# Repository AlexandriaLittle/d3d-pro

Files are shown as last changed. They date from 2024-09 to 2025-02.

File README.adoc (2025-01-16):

= D3D Pro 3D Printer

=== https://alexandrialittle.github.io/d3d-pro/[Click HERE for the Documentation Page!]

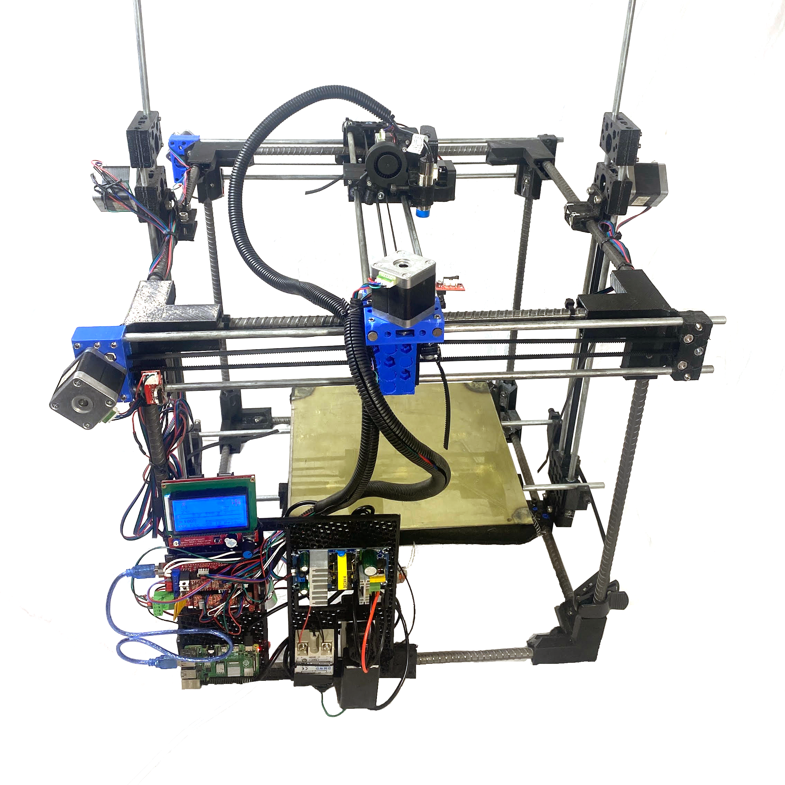
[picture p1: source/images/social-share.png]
D3D Pro 3D Printer


== How to use this project:
All of the files needed to produce the machine are in the 'source' folder. This includes the STLs for printing, the purchase list, and the firmware source code. The instructions are available https://alexandrialittle.github.io/d3d-pro/[HERE].

Modeled in Legacy DOF (Distributed Open Source Hardware Framework)

== Frequently Asked Questions:

=== Who is this printer for? Why should I build this printer?
- This printer is designed for the hobbyist, the "prosumer", and anyone who needs industrial productivity on a small scale. The D3D Pro 3D Printer is designed to be user repairable for life - i.e. not planned obsolesence / planned failure. It is made entirely from common-off-the-shelf components so that sourcing the materials for the build and for repair is easy and quick. If you need a machine that can last you your entire life, this is the one for you!

=== What features does the D3D Pro have? What is it capable of?
* The D3D Pro has automatic bed leveling, printing over WIFI, advanced Marlin firmware features including Input Shaping and Linear (Pressure) Advance, a gearless extruder with an open filament path, superior performance with flexable filaments (due to the short distance between filament drive point and melt zone), a standardized Universal Axis motion system, and much more.
* The D3D Pro is capable of printing strong, industrial quality parts quickly with good print precision and robust performance.

=== What is the print volume?
* The D3D Pro printer has a 300mm x 300mm x 350mm print volume. Is that not enough for your needs? The printer is also fully scalable!

=== What does "modular" mean for this 3D Printer?
* The D3D Pro is broken up into six modules - The Univeral Axis, the Universal Frame, the Universal Controller, the Universal Gearless Extruder, the Fast Heated Bed, and the Filament Spool Holder. These modules can be used for many things beyond just a 3D Printer, including other CNC machines, camera sliders, a personal computer, a robot controller, a miltipurpose heated surface, and more! More modules can be added to the 3D Printer to increase its performance capabilities. For example, more Universal Axes can be added to increase bed lift, additional Universal Controllers and Universal Gearless Extruders can be added for higher throughput, etc.

=== What does "fully scalable" mean for this printer?
* Because the printer uses standardized modular components, it can be modified to be much larger in size if necessary for your use case. Simply increase the size of the frame, axes rods and belts, and heated bed, extend the wires, and you're all but good to go! Additional axes can be added to the printer easily to increase the bed lift capacity or provide a more rigid axis.

=== What materials can it print?
* The printer can print any 3D Printing filament of 2.85mm or 1.75mm diameter (depending on how you build the extruder) up a maximum temperature of 285C. The heated bed surface can reach a temperature of 100C+. The has been verified to work with common printer filaments like PLA, PETG, PET, and ASA.

=== Why are all of the axes belt-driven?
* The standardized Universal Axis motion system is fully belt-driven to simplify the machine's design, make maintenance a breeze, and allow for part interchangeability.

=== Why is the frame made out of rebar?
* Rebar is an inexpensive, robust, and strong material that comes in stock lengths of up to 20'. This helps the printer scale up if necessary for litte extra cost while providing a solid frame for the machine to operate in.

=== Why is the extruder "gearless"?
* The D3D Pro uses the Universal Gearless Extruder for its open filament path, making the job of clearing any possible clogs a simple task. The gearless design is also simpler, requires less maintenance, has lower cost replacement parts, and provides superior performance with soft, flexible filaments due to the short distance between the point where the filament is driven by the extruder gear and the melt zone.

=== How fast does it print?
* With the proper slicer settings and tuning of Marlin firmware's advanced features, the printer has been able to reliably print at speeds as fast as 80mm/s - 100mm/s at an acceleration of 3000mm/s^2. (0.4mm nozzle at 0.2mm layer height)

=== What is the volumetric flow rate of the hotend?
* The D3D Pro uses a Volcano style hotend, the specifications of which can be found here: https://e3d-online.com/products/volcano-hotend[E3D Volcano Hotend Product Page]

=== What are the machine dimensions?
* (675mm Wide x 665mm Deep x 645mm Tall) without the filament spool holder
* (675mm Wide x 665mm Deep x 960mm Tall) (approx.) with the filament spool holder
* (26.5" Wide x 26" Deep x 25.25" Tall) (approx.) without filament spool holder
* (26.5" Wide x 26" Deep x 37.5" Tall) (approx.) with filament spool holder

=== I want to build one! Where can I get parts and tools?
* Many of the parts for the printer can be purchased from the local hardware store. For example, you can get the fasteners, all of the heated bed components, the rebar frame members, the rods for the Universal Axes, etc. at your local Lowe's, Menards, Home Depot, etc. Some of the more specific 3D Printer components can be sourced from online retailers like Amazon, eBay, Aliexpress, etc. All of the tools should be available at the hardware store as well! Lastly, the 3D Printed components can be printed from the source files provided (if you have access to a 3D Printer already), or ordered from a 3D printing service or a friend with a printer. :)

== Contributors
 - Alexandria Little
 - Marcin Jakubowski, Ph.D.
 - Open Source Ecology
 - Nathan Heidt
 - Sean Marquez
 - J. Simmons, Ph.D.
 - Eric Lotze (One of the original 3D printer devs)
 - Irvin Inzurriaga (Wiring Video)
 - Jean-Baptiste Vervaeck (Graphic design of original documentation template)
 - Printables User @OK1HRA_5209 - https://www.printables.com/model/716371-parameterizable-rugged-box-in-openscad[Parameterizable rugged box in OpenScad] (CC-BY-SA-4.0)
 - Marlena Nedeljkovic

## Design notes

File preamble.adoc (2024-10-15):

== Thank you for reading this documentation! 
It would mean the world to all of us who poured our time, love, and efforts into this project if you would study, share, replicate, sell, remix, manufacture, mod, or otherwise interact with the D3D Pro 3D Printer. This work is released under the https://creativecommons.org/licenses/by-sa/4.0/[Creative Commons Attribution Share-Alike 4.0 International license]. Feel free to use all of the freedoms that you are granted under that (pretty damn permissive) license. Remember to credit the contributors and share your remixes and upgrades under the same license!

== Contributors
 - Alexandria Little
 - Marcin Jakubowski, Ph.D.
 - Open Source Ecology
 - Nathan Heidt
 - Sean Marquez
 - J. Simmons, Ph.D.
 - Eric Lotze (One of the original 3D printer devs)
 - Irvin Inzurriaga (Wiring Video)
 - Jean-Baptiste Vervaeck (Graphic design of original documentation template)
 - Printables User @OK1HRA_5209 - https://www.printables.com/model/716371-parameterizable-rugged-box-in-openscad[Parameterizable rugged box in OpenScad] (CC-BY-SA-4.0)
 - Marlena Nedeljkovic
 
== A note on tool substitution
There are a lot of tools listed as 'required' in this project, but many of them can be substituted for other, simpler tools. If you do not have access to all of the nice-to-have tools that are listed in this project, feel free to adapt the instructions to what you have on hand. Please remember to be safe and use common sense!

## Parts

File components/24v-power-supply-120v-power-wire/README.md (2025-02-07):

TODO: USE EITHER 18AWG OR 20AWG WIRE FOR 120v AC

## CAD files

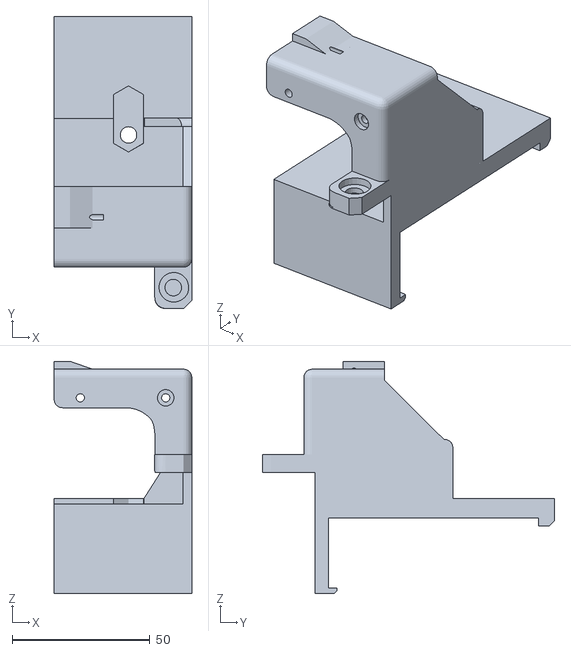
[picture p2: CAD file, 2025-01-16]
source/printed_parts/14-Extruder Main.stl
50.0 x 106.0 x 84.4

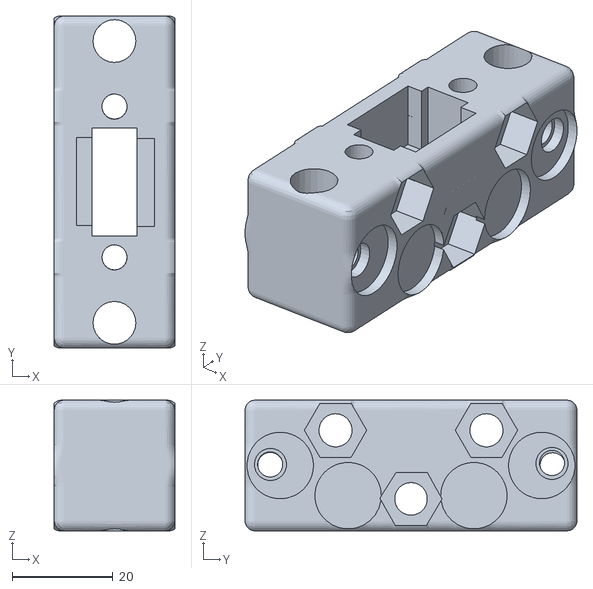
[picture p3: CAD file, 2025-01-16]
source/printed_parts/11-Idler.stl
24.0 x 66.0 x 26.0

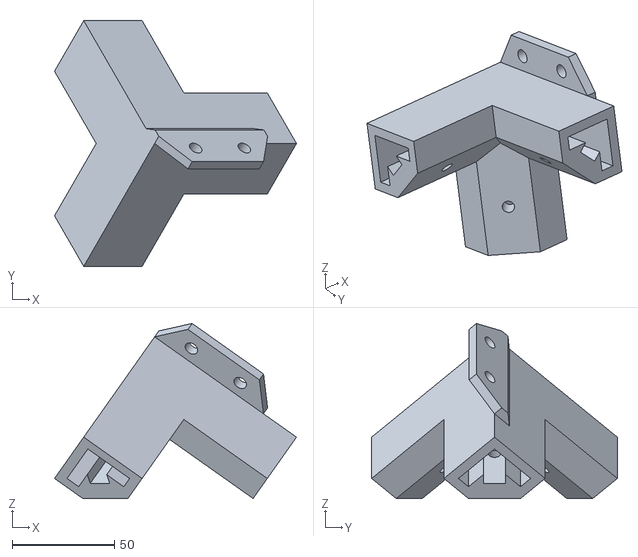
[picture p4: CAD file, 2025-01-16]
source/printed_parts/2-Corner Connector Left.stl
118.4 x 120.2 x 85.6

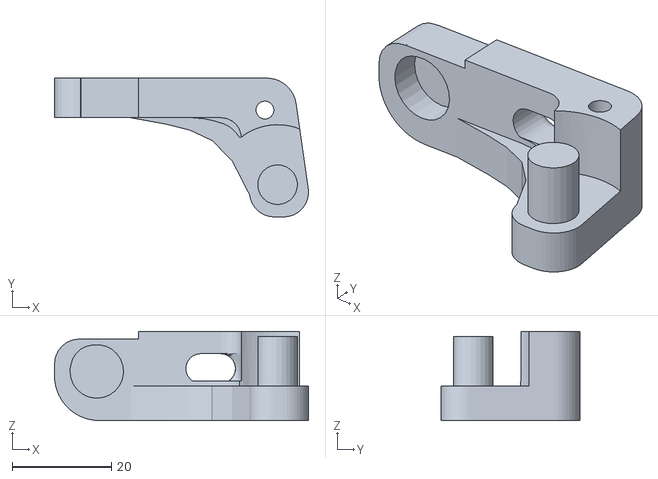
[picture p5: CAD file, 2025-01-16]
source/printed_parts/16-Extruder Tensioner.stl
51.2 x 28.0 x 18.0

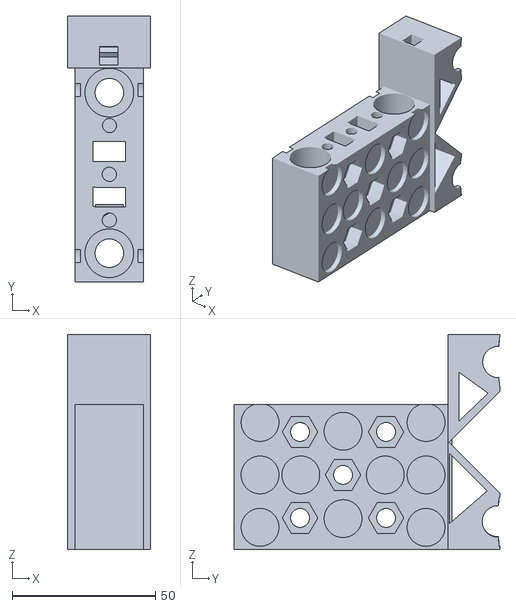
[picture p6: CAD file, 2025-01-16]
source/printed_parts/9-Y2 Carriage.stl
29.0 x 92.7 x 75.0

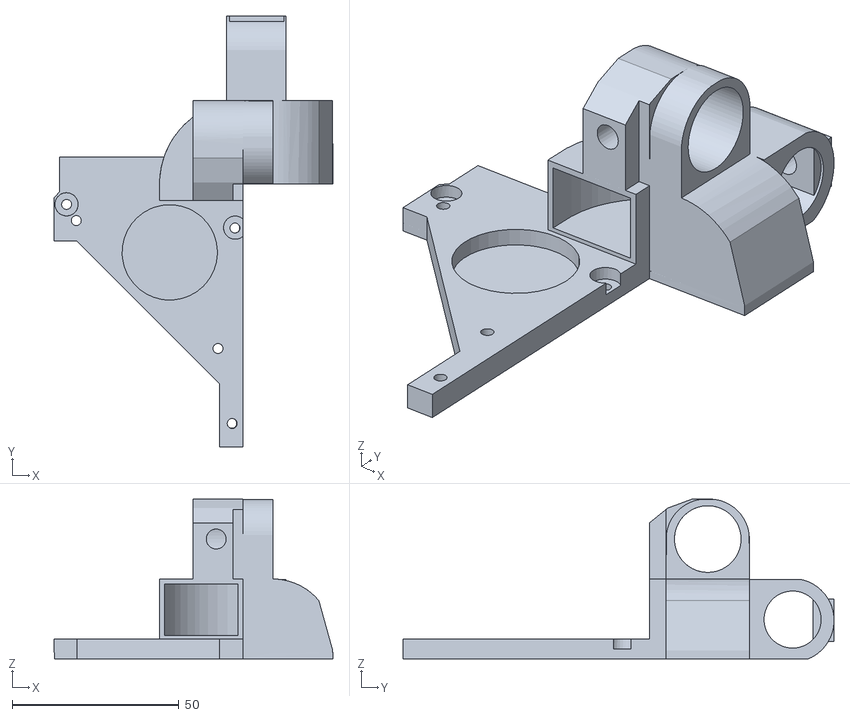
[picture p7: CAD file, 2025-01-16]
source/printed_parts/15-Extruder Secondary.stl
83.6 x 129.4 x 48.0

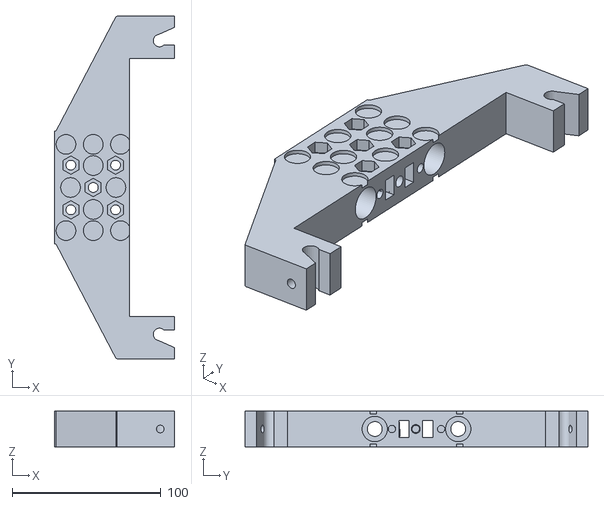
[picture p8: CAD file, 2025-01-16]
source/printed_parts/7-Z Carriage.stl
80.6 x 229.9 x 24.0

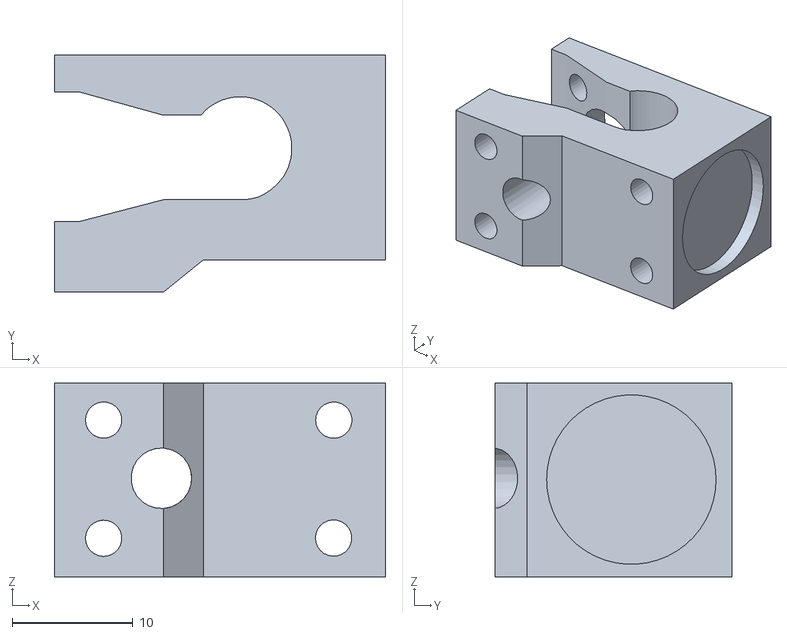
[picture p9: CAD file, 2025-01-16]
source/printed_parts/12-Autoparallel Clip.stl
27.4 x 19.6 x 16.0

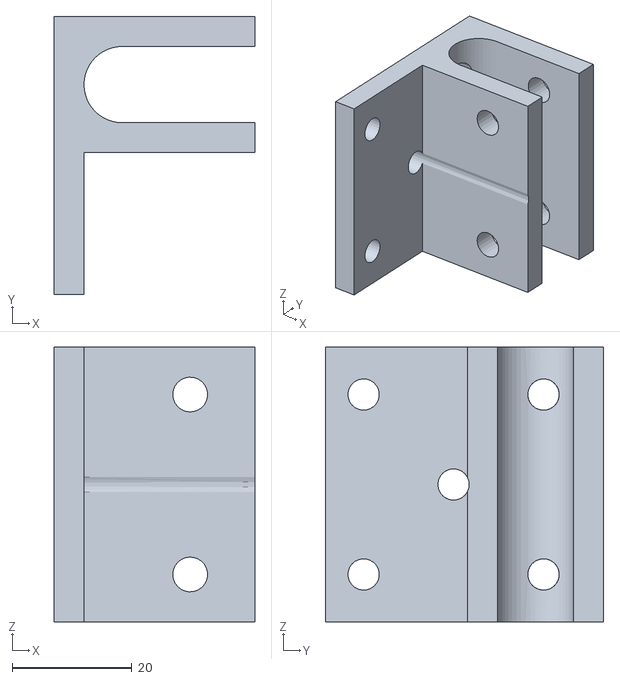
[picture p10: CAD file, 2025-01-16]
source/printed_parts/4-Universal Frame Rebar Mount.stl
33.5 x 46.4 x 45.8

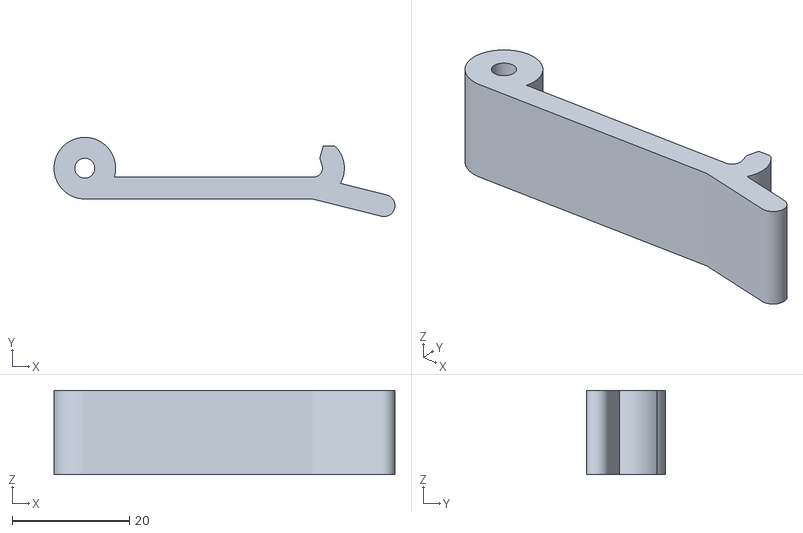
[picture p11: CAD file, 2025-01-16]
source/printed_parts/22-Control Panel Electrical Box Clip.stl
58.1 x 13.5 x 14.4

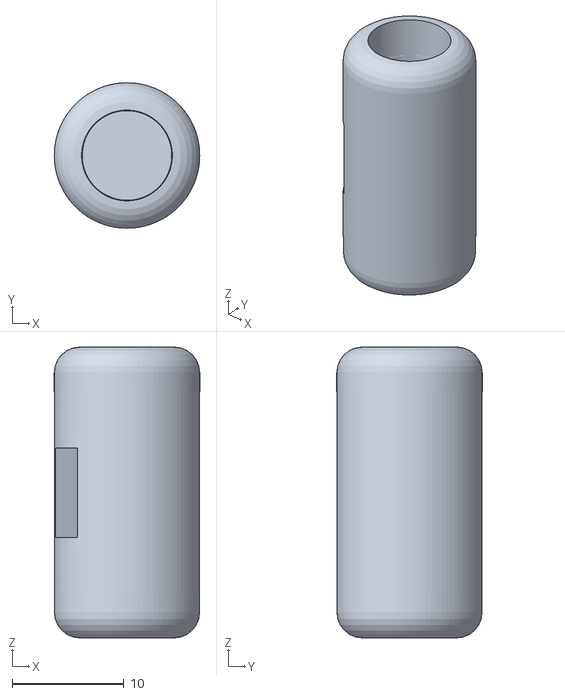
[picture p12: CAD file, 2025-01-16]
source/printed_parts/17-Belt Cylinder.stl
13.0 x 13.0 x 26.0

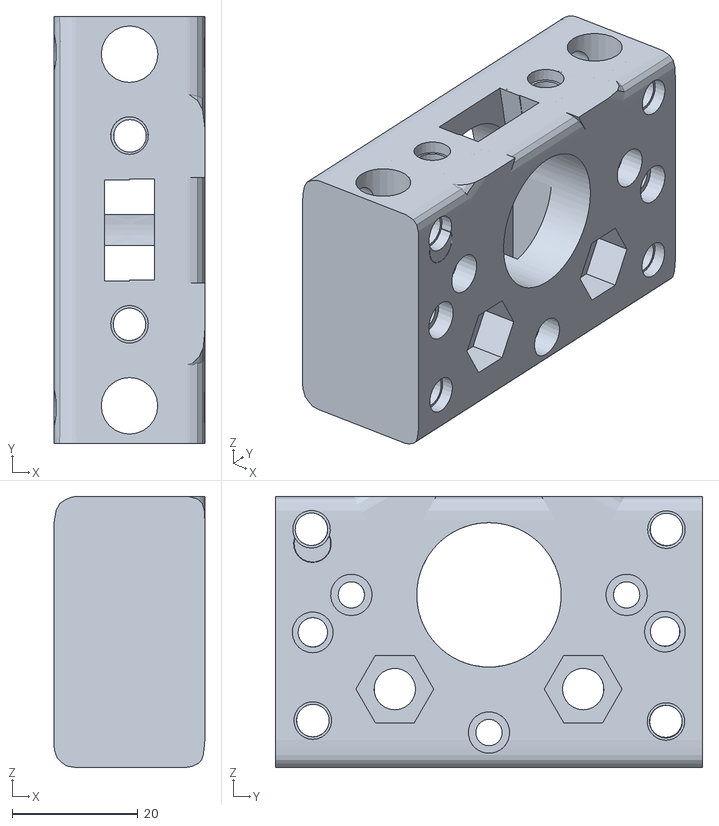
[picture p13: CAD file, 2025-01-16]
source/printed_parts/5-Motor piece.stl
24.0 x 68.0 x 43.2

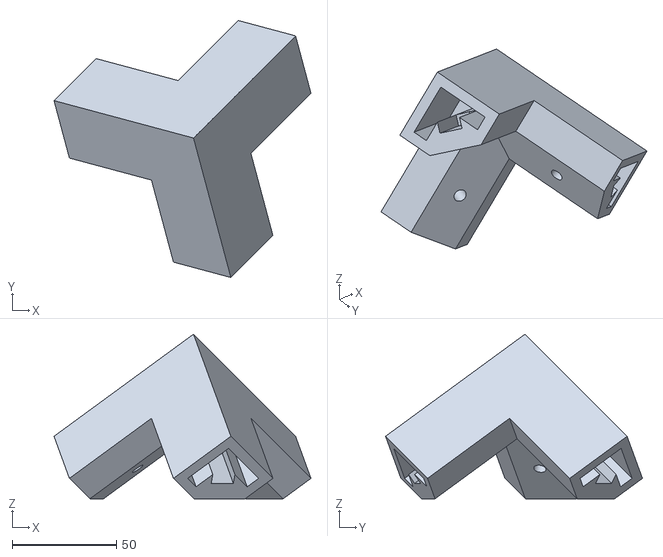
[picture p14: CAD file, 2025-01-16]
source/printed_parts/1-Corner Connector.stl
123.5 x 123.5 x 79.1

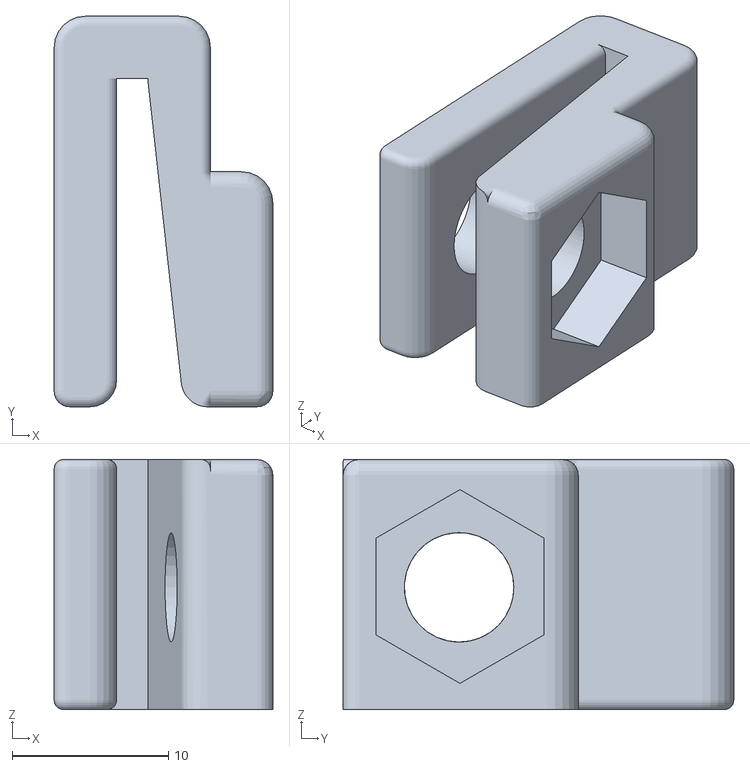
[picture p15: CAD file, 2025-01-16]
source/printed_parts/18-Belt Clamp.stl
14.0 x 25.0 x 16.0

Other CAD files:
source/printed_parts/3-Corner Connector Right.stl
source/printed_parts/8-Y1 Carriage.stl
source/printed_parts/10-Carriage Closure.stl
source/printed_parts/6-Carriage.stl
source/printed_parts/13-Bed Holder.stl
source/printed_parts/19-Control Panel.stl

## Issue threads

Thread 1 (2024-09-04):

Finish Universal Controller assembly steps

AlexandriaLittle, 2024-09-04:

AlexandriaLittle, 2024-09-05:
Completed breaking down into major steps

AlexandriaLittle, 2024-09-11:
Custom wires list:
• RAMPS 1.4 to RAMPS 1.4 power connection (24v)
• RAMPS 1.4 to Solid State Relay (24v signal for heated bed)
• Inductive Probe to RAMPS 1.4 wire extension (5v)
• 40mm Extruder Fan to RAMPS 1.4 wire extension (24v)
• GFCI to 24v Industrial Power Module (120vac)
• GFCI to Heated Bed/Solid State Relay (120vac)

AlexandriaLittle, 2024-09-12:
Verify parts quantity used for ferrules, fork terminals, etc.

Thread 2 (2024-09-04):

Add additional assembly steps to Halogen Lightbulb Assembly

AlexandriaLittle, 2024-09-04:
* Add list of steps for insulating soldered connections
* Add steps for securing the assembly with metal zip ties

AlexandriaLittle, 2024-09-20:
Completed per commit b2dc15a

Closed 2024-09-20.

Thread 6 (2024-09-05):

Add fuse and on/off switch to components and Universal Controller

AlexandriaLittle, 2024-09-05:

AlexandriaLittle, 2024-09-15:
Changed switch size to 19mm (3/4") round for more standard size

AlexandriaLittle, 2024-10-15:
Closed due to instructions being added (some time ago)

Closed 2024-10-15.

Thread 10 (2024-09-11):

Add note above tools BOM for alternative tool choices

AlexandriaLittle, 2024-09-11:

AlexandriaLittle, 2024-09-11:
Possible implementation: use the tools notes functionality that currently exists to specify possible alternative tools

AlexandriaLittle, 2024-09-20:
Closed as of commit 3d84411

Closed 2024-09-20.

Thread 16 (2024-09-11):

Gather software licenses for OSHWA Cert release

AlexandriaLittle, 2024-09-11:

AlexandriaLittle, 2024-09-11:
Required:
* Marlin Firmware
* OctoPi / Octoprint

Nice to have:
* Raspberry pi imager
* Arduino IDE
* Slicer software

AlexandriaLittle, 2024-09-11:
Marlin - GPL-3.0
Octoprint - AGPL-3.0

Closed 2024-09-15.

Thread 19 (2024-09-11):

Finish Universal Gearless Extruder custom wiring assembly steps & pictures

AlexandriaLittle, 2024-09-11:

AlexandriaLittle, 2024-10-15:
Custom wiring assembly steps are complete. Skipping pictures for now.

Closed 2024-10-15.

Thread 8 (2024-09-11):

Define when the documentation is sufficiently completed for this project

AlexandriaLittle, 2024-09-11:

AlexandriaLittle, 2024-09-11:
* An average of 1 image per assembly step

AlexandriaLittle, 2024-09-11:
* The machine can be assembled entirely from common-off-the-shelf (COTS) goods and tools.

AlexandriaLittle, 2024-09-11:
* No custom parts need to be manufactured by someone other than the user if all tools listed in the BOM are used.

AlexandriaLittle, 2024-09-11:
* All open source software is used.

AlexandriaLittle, 2024-10-15:
Certification will be sought after all of the textual instructions are complete and the FreeCAD source files are in place

AlexandriaLittle, 2024-10-15:
I will include more pictures later. Text instructions will work for the initial certification.

Closed 2024-10-15.

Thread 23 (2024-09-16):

Improve the 24v power supply usage instructions in the Hot End Assembly component

AlexandriaLittle, 2024-09-16:

AlexandriaLittle, 2025-01-31:
Completed per commit d162ce39c4c8891f3799ca9238b5f6ade1c71304

AlexandriaLittle, 2025-01-31:
Added short note to explain that the Universal Controller can be used in place of the 24v Power Supply component. Completed per commit bf1e8d1

Closed 2025-01-31.

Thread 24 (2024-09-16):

Change all of the instances of 'screw into plastic' to include fully screwing through the component

AlexandriaLittle, 2024-09-16:
If the screw is only partially screwed through when tightening takes place it is much more likely to strip the plastic.

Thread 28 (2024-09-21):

Add assembly steps to the Universal Frame to twist the frame square by using a flat surface

AlexandriaLittle, 2024-09-21:
This is especially useful if a corner component is slightly too tight and the rebar could only be inserted in one orientation.

AlexandriaLittle, 2024-09-23:
Alternatively, use a long bar clamp to squeeze the corners together. This method is more effective than pushing against the work surface.

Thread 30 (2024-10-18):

Add all subcomponents to BOM generation

AlexandriaLittle, 2024-10-18:
Fix missing modules in Bill of Materials table

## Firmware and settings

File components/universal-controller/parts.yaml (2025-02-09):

ramps-board-assembly:
  description: RAMPS Board Assembly
  id: ramps-board-assembly
  notes: ''
  options:
    - ramps-1_4-board-assembly
  quantity: 1
  quantityUnits: module
  selectedOption: 0
electrical-tape:
  description: Electrical Tape
  id: electrical-tape
  notes: ''
  options:
    - electrical-tape
  quantity: 1
  quantityUnits: as needed
  selectedOption: 0
16gb-microsd-card:
  description: 16GB MicroSD Card
  id: 16gb-microsd-card
  notes: ''
  options:
    - 16gb-microsd-card
  quantity: 1
  quantityUnits: part
  selectedOption: 0
24v-power-supply:
  description: 24v Power Supply Module
  id: 24v-power-supply
  notes: ''
  options:
    - 24v-power-supply
  quantity: 1
  quantityUnits: part
  selectedOption: 0
electrical-cord:
  description: Three Prong Electrical Cord
  id: electrical-cord
  notes: ''
  options:
    - electrical-cord-nema-5-15p
  quantity: 1
  quantityUnits: part
  selectedOption: 0
electrical-plug:
  description: Two Prong Electrical Plug
  id: electrical-plug
  notes: ''
  options:
    - electrical-plug-nema-1-15
  quantity: 1
  quantityUnits: part
  selectedOption: 0
solder:
  description: Electrical Solder
  id: solder
  notes: ''
  options:
    - electrical-solder
  quantity: 1
  quantityUnits: application(s)
  selectedOption: 0
ferrule:
  description: Ferrule
  id: ferrule
  notes: ''
  options:
    - ferrule
  quantity: 20
  quantityUnits: part(s)
  selectedOption: 0
gfci:
  description: GFCI
  id: gfci
  notes: ''
  options:
    - ground-fault-connection-interrupter
  quantity: 1
  quantityUnits: part
  selectedOption: 0
heat-shrink-tubing:
  description: Heat Shrink Tubing
  id: heat-shrink-tubing
  notes: ''
  options:
    - heat-shrink-tubing
  quantity: 1
  quantityUnits: part
  selectedOption: 0
lever-wire-nut:
  description: Lever Wire Nut
  id: lever-wire-nut
  notes: ''
  options:
    - lever-wire-nut
  quantity: 1
  quantityUnits: part
  selectedOption: 0
microsd-to-sd-card-adapter:
  description: MicroSD to SD Card Adapter
  id: microsd-to-sd-card-adapter
  notes: ''
  options:
    - microsd-to-sd-card-adapter
  quantity: 1
  quantityUnits: part
  selectedOption: 0
raspberry-pi:
  description: Raspberry Pi Computer
  id: raspberry-pi
  notes: 'The Raspberry Pi is an optional component that enables extra features like wireless printing. It is not strictly required, as gcode files can be loaded into the printer via an SD card.'
  options:
    - raspberry-pi-4b
  quantity: 1
  quantityUnits: part
  selectedOption: 0
reprap-controller:
  description: RepRap Discount Full Graphic Smart Controller
  id: reprap-controller
  notes: ''
  options:
    - reprap-discount-full-graphic-smart-controller
  quantity: 1
  quantityUnits: part
  selectedOption: 0
solid-state-relay:
  description: Solid State Relay (SSR)
  id: solid-state-relay
  notes: ''
  options:
    - solid-state-relay
  quantity: 1
  quantityUnits: part
  selectedOption: 0
split-wire-loom:
  description: Split Wire Loom
  id: split-wire-loom
  notes: ''
  options:
    - split-wire-loom
  quantity: 1
  quantityUnits: part
  selectedOption: 0
case:
  description: Universal Controller Case
  id: case
  notes: ''
  options:
    - universal-controller-case
  quantity: 1
  quantityUnits: part
  selectedOption: 0
zip-tie-large:
  description: Large Zip Tie
  id: zip-tie-large
  notes: ''
  options:
    - zip-tie-large
  quantity: 20
  quantityUnits: part(s)
  selectedOption: 0
zip-tie-small:
  description: Small Zip Tie
  id: zip-tie-small
  notes: ''
  options:
    - zip-tie-small
  quantity: 20
  quantityUnits: part(s)
  selectedOption: 0
jumper:
  description: Jumper Cap
  id: jumper
  notes: ''
  options:
    - 2_54mm-jumper-cap
  quantity: 15
  quantityUnits: part(s)
  selectedOption: 0
10-pin-idc-connector:
  description: 10 Pin IDC Conector
  id: 10-pin-idc-connector
  notes: ''
  options:
    - 10-pin-idc-connector
  quantity: 2
  quantityUnits: part(s)
  selectedOption: 0
marlin-firmware:
  description: Marlin Firmware
  id: marlin-firmware
  notes: ''
  options:
    - marlin-firmware
  quantity: 1
  quantityUnits: image
  selectedOption: 0
raspberry-pi-image:
  description: Octoprint Raspberry Pi Software Image
  id: raspberry-pi-image
  notes: ''
  options:
    - octoprint-raspberry-pi-software-image
  quantity: 1
  quantityUnits: image
  selectedOption: 0
fork-terminal:
  description: Fork Terminal
  id: fork-terminal
  notes: ''
  options:
    - electrical-fork-terminal
  quantity: 4
  quantityUnits: part(s)
  selectedOption: 0
2-pin-dupont-connector:
  description: 2 Pin Female Dupont Connector
  id: 2-pin-dupont-connector
  notes: ''
  options:
    - 2-pin-dupont-connector
  quantity: 1
  quantityUnits: part(s)
  selectedOption: 0
3-pin-dupont-connector:
  description: 3 Pin Female Dupont Connector
  id: 3-pin-dupont-connector
  notes: ''
  options:
    - 3-pin-dupont-connector
  quantity: 1
  quantityUnits: part(s)
  selectedOption: 0
4-pin-dupont-connector:
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

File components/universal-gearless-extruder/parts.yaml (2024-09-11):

40mm-fan:
  description: 40mm Fan
  id: 40mm-fan
  notes: ''
  options:
    - 24v-40mm-fan
  quantity: 1
  quantityUnits: part
  selectedOption: 0
40mm-heatsink:
  description: 40mm Heatsink Fins
  id: 40mm-heatsink
  notes: ''
  options:
    - mk7-mk8-40mm-heatsink
  quantity: 1
  quantityUnits: part
  selectedOption: 0
608-bearing:
  description: 608 ZZ Bearing
  id: 608-bearing
  notes: ''
  options:
    - 608-bearing
  quantity: 1
  quantityUnits: part
  selectedOption: 0
active-cooling-height-sensor-plotter:
  description: Secondary Extruder Part
  id: active-cooling-height-sensor-plotter
  notes: 3D Printed Part
  options:
    - universal-gearless-extruder-active-cooling-height-sensor-plotter
  quantity: 1
  quantityUnits: part
  selectedOption: 0
blower-fan:
  description: Blower Fan
  id: blower-fan
  notes: ''
  options:
    - 24v-5015-blower-fan
  quantity: 1
  quantityUnits: part
  selectedOption: 0
extruder-gear:
  description: Filament Drive Gear
  id: extruder-gear
  notes: ''
  options:
    - mk7-extruder-drive-gear
  quantity: 1
  quantityUnits: part
  selectedOption: 0
extruder-spring:
  description: Extruder Spring
  id: extruder-spring
  notes: ''
  options:
    - 10mm-od-35mm-spring
  quantity: 1
  quantityUnits: part
  selectedOption: 0
height-sensor:
  description: Height Sensor
  id: height-sensor
  notes: ''
  options:
    - height-sensor
  quantity: 1
  quantityUnits: part
  selectedOption: 0
hot-end-assembly:
  description: Hot End Assembly
  id: hot-end-assembly
  notes: ''
  options:
    - hot-end-assembly
  quantity: 1
  quantityUnits: part
  selectedOption: 0
m3-20mm-screw:
  description: M3 x 20mm Screw
  id: m3-20mm-screw
  notes: ''
  options:
    - m3-20mm-socket-head-cap-screw
  quantity: 4
  quantityUnits: part(s)
  selectedOption: 0
m3-30mm-screw:
  description: M3 x 30mm Screw
  id: m3-30mm-screw
  notes: ''
  options:
    - m3-30mm-socket-head-cap-screw
  quantity: 2
  quantityUnits: part(s)
  selectedOption: 0
m3-8mm-screw:
  description: M3 x 8mm Screw
  id: m3-8mm-screw
  notes: ''
  options:
    - m3-8mm-socket-head-cap-screw
  quantity: 4
  quantityUnits: part(s)
  selectedOption: 0
m3-16mm-screw:
  description: M3 x 16mm Screw
  id: m3-16mm-screw
  notes: ''
  options:
    - m3-16mm-socket-head-cap-screw
  quantity: 2
  quantityUnits: part(s)
  selectedOption: 0
m6-25mm-screw:
  description: M6 x 25mm Screw
  id: m6-25mm-screw
  notes: ''
  options:
    - m6-25mm-socket-head-cap-screw
  quantity: 1
  quantityUnits: part(s)
  selectedOption: 0
m6-nut:
  description: M6 Nut
  id: m6-nut
  notes: ''
  options:
    - m6-nut
  quantity: 1
  quantityUnits: part
  selectedOption: 0
motor-mount:
  description: Motor Mount
  id: motor-mount
  notes: 3D Printed Part
  options:
    - universal-gearless-extruder-motor-mount
  quantity: 1
  quantityUnits: part
  selectedOption: 0
split-wire-loom:
  description: 2 Meter Split Wire Loom
  id: split-wire-loom
  notes: ''
  options:
    - split-wire-loom
  quantity: 1
  quantityUnits: part
  selectedOption: 0
spring-tensioner:
  description: Spring Tensioner Arm
  id: spring-tensioner
  notes: 3D printed part
  options:
    - universal-gearless-extruder-spring-tensioner-arm
  quantity: 1
  quantityUnits: part
  selectedOption: 0
stepper-motor:
  description: Nema 17 Stepper Motor
  id: stepper-motor
  notes: ''
  options:
    - nema-17-0_5nm-stepper-motor
  quantity: 1
  quantityUnits: part
  selectedOption: 0
stepper-motor-cable:
  description: 2 Meter Stepper Motor Cable
  id: stepper-motor-cable
  notes: ''
  options:
    - stepper-motor-cable
  quantity: 1
  quantityUnits: part
  selectedOption: 0
thermal-paste:
  description: Thermal Paste
  id: thermal-paste
  notes: ''
  options:
    - thermal-paste
  quantity: 2
  quantityUnits: drop(s)
  selectedOption: 0
zip-tie-small:
  description: Small Zip Tie
  id: zip-tie-small
  notes: ''
  options:
    - zip-tie-small
  quantity: 1
  quantityUnits: part
  selectedOption: 0
22awg-wire:
  description: 22AWG Wire
  id: 22awg-wire
  notes: ''
  options:
    - 22awg-wire
  quantity: 2000
  quantityUnits: mm
  selectedOption: 0
ferrule:
  description: Ferrule
  id: ferrule
  notes: ''
  options:
    - ferrule
  quantity: 2
  quantityUnits: part
  selectedOption: 0

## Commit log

2019-03-07 initial upload of trrs-wssm
    [UpperHalf.stl, sensor-jig.stl, trrs-wssm-housing-base.stl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]
2019-03-13 Add empty assembly steps to top level component
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2019-03-17 Add assembly instructions
    [trrs-wssm-housing-top.stl, trrs-wssm-housing.f3d, trrs-wssm-jig.f3d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]
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2019-04-01 Include github imagedir macro so images render in assembly instructions
2022-03-02 fix dof-helper for generating assemblyInstructions
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2024-08-19 Renamed extruder gear to Mk7 Extruder Drive Gear
2024-08-21 Rename heatsink to Universal Gearless Extruder Heatsink Block
2024-08-21 Rename heater block to Volcano Style Heater Block Generic
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2024-08-21 Renamed heater cartridge to 24V 70W Heater Cartridge
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2024-08-21 Add M3 x 30mm Socket Head Cap Screw
2024-08-21 Add M3 x 20mm Socket Head Cap Screw
2024-08-21 Add M3 x 8mm Socket Head Cap Screw
2024-08-21 Add Universal Gearless Extruder Active Cooling Height Sensor Plotter Part
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2024-08-23 Rename Volcano Style Heater Block Generic to Volcano Heater Block Assembly
2024-08-23 Add M3 4mm Grub Screw and Volcano Heater Block components
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2024-08-23 Move components to hot end assembly and add instructions
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2024-08-24 Add Slip Joint Pliers component
    [parts.yaml, tools.yaml]
2024-08-24 Add Needle Nose Pliers component and additional assembly steps
2024-08-25 Add Thermal Paste component and more assembly instructions
2024-08-25 Add and separate assembly steps for Hot End Assembly
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2024-08-25 Add Height Sensor component and more assembly instructions
2024-08-25 Add symbolic link for Universal Gearless Extruder subcomponent
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2024-08-25 Add more parts and assembly steps to Universal Gearless Extruder
2024-08-25 Add Hobby Knife component and more assembly steps for UGE
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2024-08-25 Add assembly steps to UGE for Hot End Assembly installation
2024-08-25 Add assembly instructions for extruder gear and hot end assembly adjustment
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2024-08-25 Add 5mm Allen Wrench and M6 x 25mm Screw Components and more assembly instructions
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2024-08-25 Add Split Wire Loom and Stepper Motor Cable components
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2024-08-25 Add symlinks for Motor and Idler Side modules
2024-08-25 Add parts to Motor and Idler Side components
2024-08-25 Add Universal Controller and Fast Heated Bed components
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2024-08-25 Add parts to Universal Frame, Fix Typos, Add more assembly instructions
    [parts.yaml, tools.yaml]
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2024-08-26 Add Corner Brace component, Add parts to Fast Heated Bed
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2024-08-26 Add tools for Fast Heated Bed Top Plate component
2024-08-26 Add Vise Grip Pliers component, Add assembly instructions to Fast Heated Bed Top Plate component
2024-08-26 Add assembly instructions to Fast Heated Bed Top Plate component
2024-08-26 Add parts and tools for Fast Heated Bed Bottom Plate component
2024-08-26 Add Metal File component, Add assembly instructions for Fast Heated Bed Bottom Plate
2024-08-26 Add Circular Saw and Metal Cutoff Wheel components
2024-08-26 Add parts, tools, assembly instructions for Lightbulb Assembly component
2024-08-26 Add Paper Towels component, Add assembly instructions for Lightbulb Assembly component
2024-08-26 Fix typos in Lightbulb Assembly assembly steps
2024-08-26 Add tools and precautions to Fast Heated Bed component
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2024-08-26 Add parts and tools for Motor Side Assembly component
2024-08-26 Add symlinks for parts and tools for Motor Side Assembly component
2024-08-26 Add parts, tools, and assembly steps for Motor Side Assembly component
2024-08-26 Add tools and parts for Idler Side Assembly component
2024-08-26 Add assembly instructions for Idler Side Assembly component
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2024-08-26 Add parts, tools, symlinks, and assembly instructions for Universal Axis X component.
2024-08-26 Add parts, tools, symlinks, and assembly steps for Universal Axis Y1 component
2024-08-26 Add parts, tools, symlinks, and assembly instructions for the Universal Axis Y2 component
2024-08-26 Add Volcano Heater Block Sock component to Hot End Assembly component instructions and parts
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2024-08-29 Add tools, parts, syminks, assembly instructions to Carbon Fiber Blanket Sleeve component
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2024-08-30 Make Universal Controller component a required tool of the Fast Heated Bed component
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2024-08-30 Correct a tool size in Universal Gearless Extruder parts and assembly steps
    [tools.yaml]
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2024-08-30 Update component in UGE for correct fit
    [parts.yaml, tools.yaml]
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2024-08-30 Update assemblySteps.yaml
    Fix typo
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2024-09-01 Add image details to Universal Axis Motor Side Assembly component assembly instructions
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2024-09-01 Fix incorrect image file names in assembly steps
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2024-09-10 Remove extra unneeded part causing an error
    [parts.yaml]
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2024-09-12 Fix missing name for Stepper Motor Driver Heatsink component
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2024-09-20 Refactor Universal Frame component assembly instrucitons to include the Universal Frame Top and the Universal Frame base
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2024-09-20 Fix typos in tool BOM
    [tools.yaml]
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2024-09-20 Add parts, tools, and assembly steps to Fast Heated Bed Lightbulb Assembly component
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2024-09-20 Add short line to Lightbulb Assembly component assembly instructions
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2024-10-14 Add components and assembly steps for Universal Gearless Extruder Heatsink Block component
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2024-10-14 Add missing component to Universal Controller component parts
    [parts.yaml]
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2024-10-15 Add additional tools and assembly steps for Universal Gearless Extruder Heatsink Block component
2024-10-15 Add tool and assembly steps for Universal Gearless Extruder Heatsink Block component
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2025-01-16 Add STL files for 3D printing to source folder
    [1-Corner Connector.stl, 10-Carriage Closure.stl, 11-Idler.stl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]
2025-01-16 Add Fast Heated Bed Plate Jig template file and steps to reproduce
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2025-01-31 Fix incorrect term in RAMPS 1.4 Assembly Steps
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2025-02-07 Fix missing component name in stepper driver precautions
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2025-02-07 Shorten final line of RAMPS Assembly Power Wire assembly steps
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2025-02-07 Add RAMPS Board Assembly Heated Bed Signal Wire component and assembly steps
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2025-02-07 Fix broken package.json for Universal Controller Electrical Plug component
    [parts.yaml]
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2025-02-07 Fix missing accent in 24v Power Supply 120v Power Wire assembly steps
2025-02-07 Add TODO for wire thickness issue
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2025-02-07 Add parts, tools, assembly steps for Fast Heated Bed 120v Power Wire component
2025-02-07 Add missing symlinks, add part to Universal Controller Electrical Plug parts list
    [parts.yaml]
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2025-02-08 Add small TODO to Universal Controller 120v Power Cord component assembly steps
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2025-02-18 Add missing tool to Universal Controller 120v Power Cord component
    [tools.yaml]
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
